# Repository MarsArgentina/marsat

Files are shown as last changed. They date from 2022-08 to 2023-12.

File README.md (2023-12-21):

# MARSAT

Marsat is an open source project aimed at developing a platform to send student experiments to the upper atmosphere. It's intended to provide it's users the following functionalities:

* GPS tracking

* APRS telemetry

* Flight computer

* Flight termination system

* Parachute

* Battery and energy management

* Bi-directional 900 MHz data link

Experiments are mounted in the upper half of the structure and must comply with 1U cubesat dimmensios. 

The system can provide conectivity and power for up to two 1/2U experiments. 

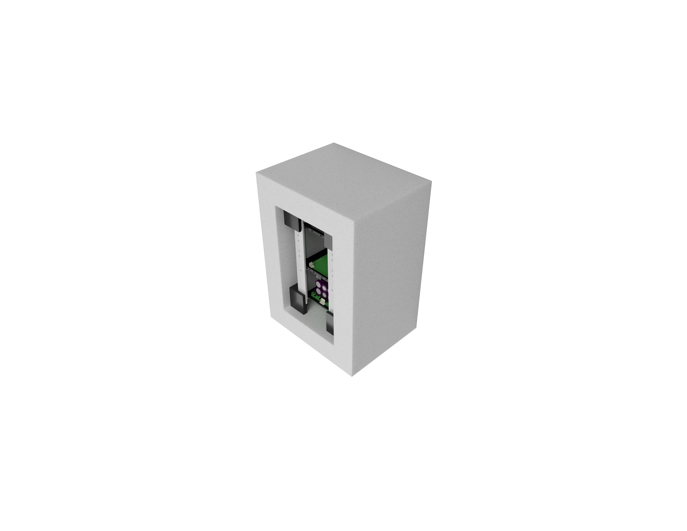
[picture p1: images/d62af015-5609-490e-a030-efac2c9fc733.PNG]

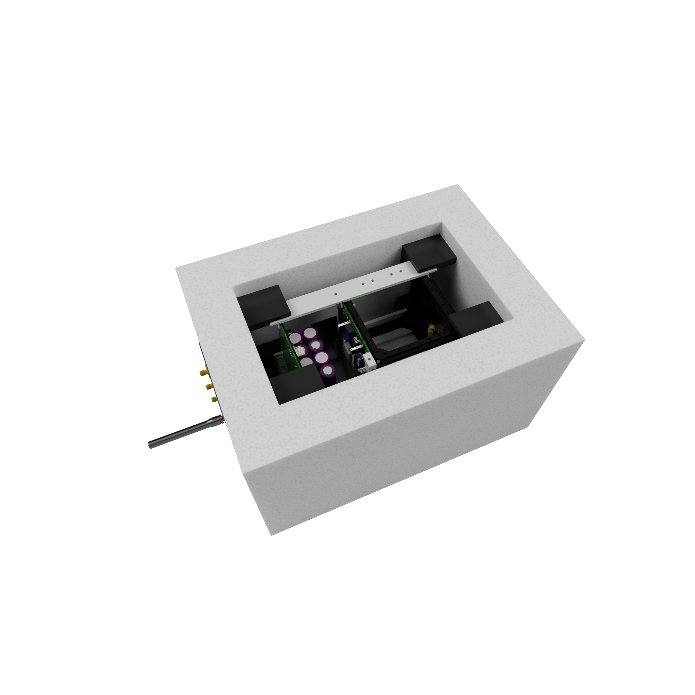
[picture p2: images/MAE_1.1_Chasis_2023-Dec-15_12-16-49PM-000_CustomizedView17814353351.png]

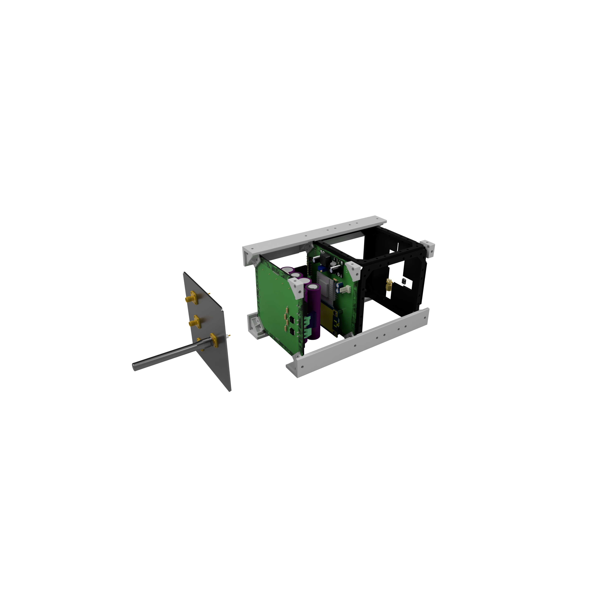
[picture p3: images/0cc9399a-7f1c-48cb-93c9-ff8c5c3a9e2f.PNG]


# Launch and Results 

Balloon was launched on December 16 of 2022, flying to 14KM until the on board computer termiated the flight due to excedinbg the configured geofense. 

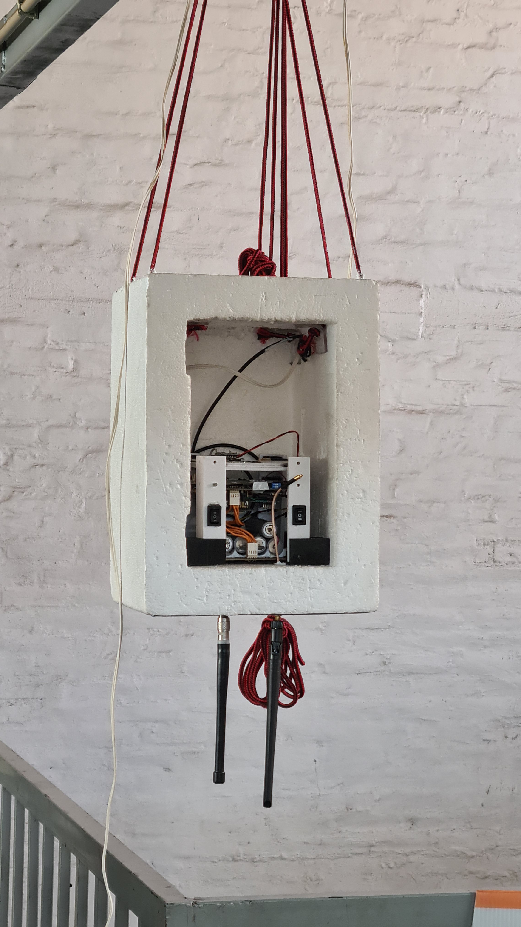
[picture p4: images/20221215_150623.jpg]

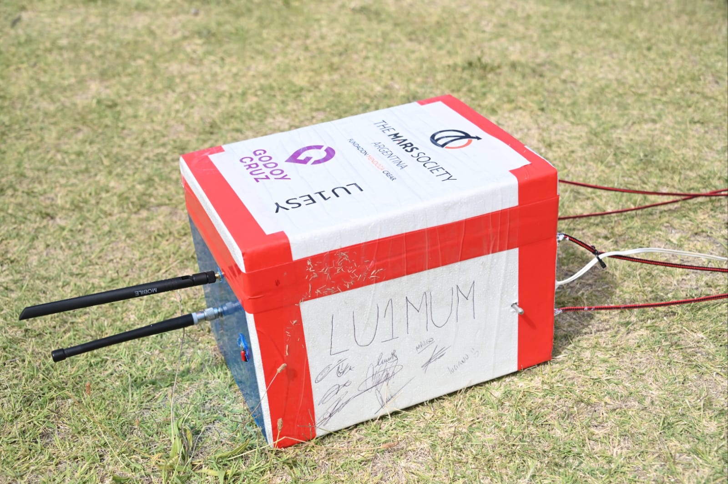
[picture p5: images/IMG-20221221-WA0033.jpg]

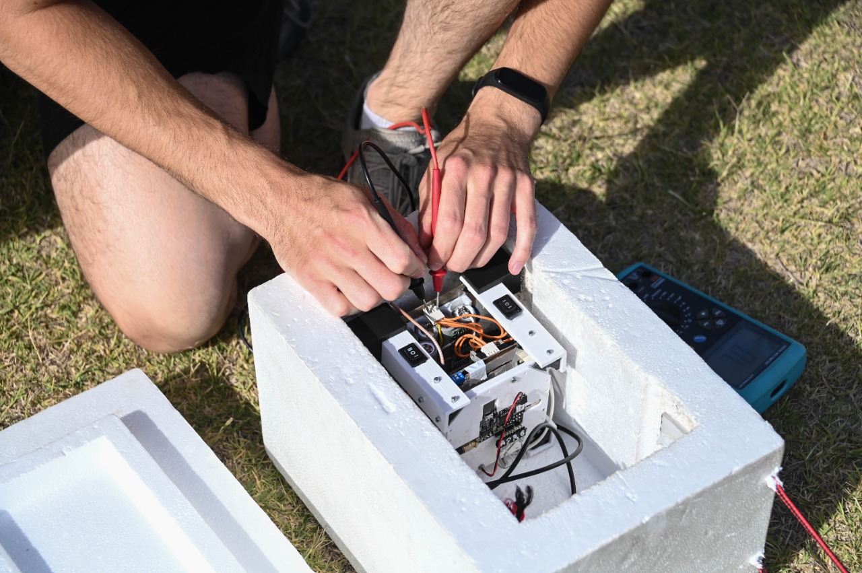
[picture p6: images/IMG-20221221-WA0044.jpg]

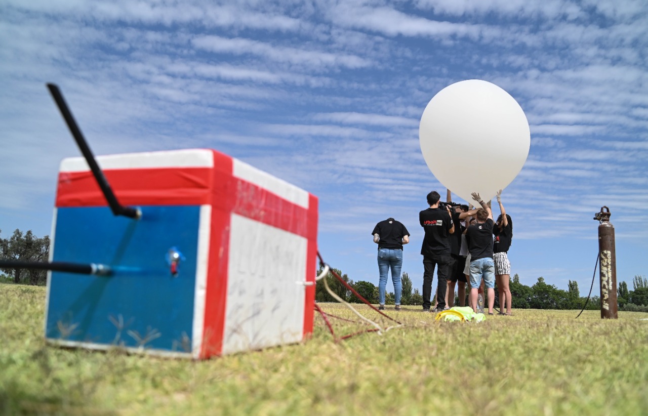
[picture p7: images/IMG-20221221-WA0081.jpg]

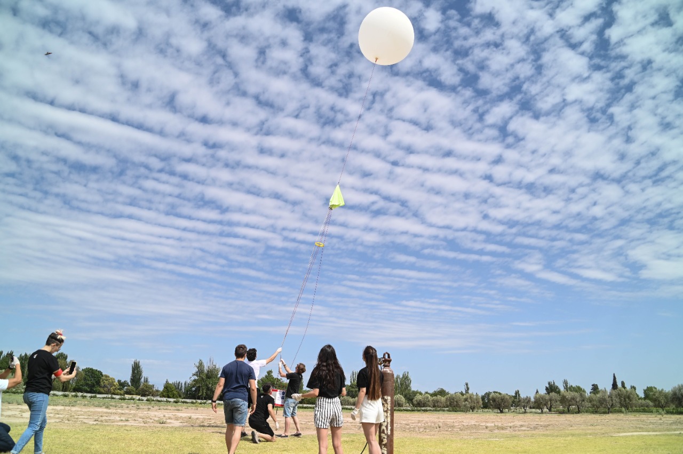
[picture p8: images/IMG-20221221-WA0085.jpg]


Some aquiered data:

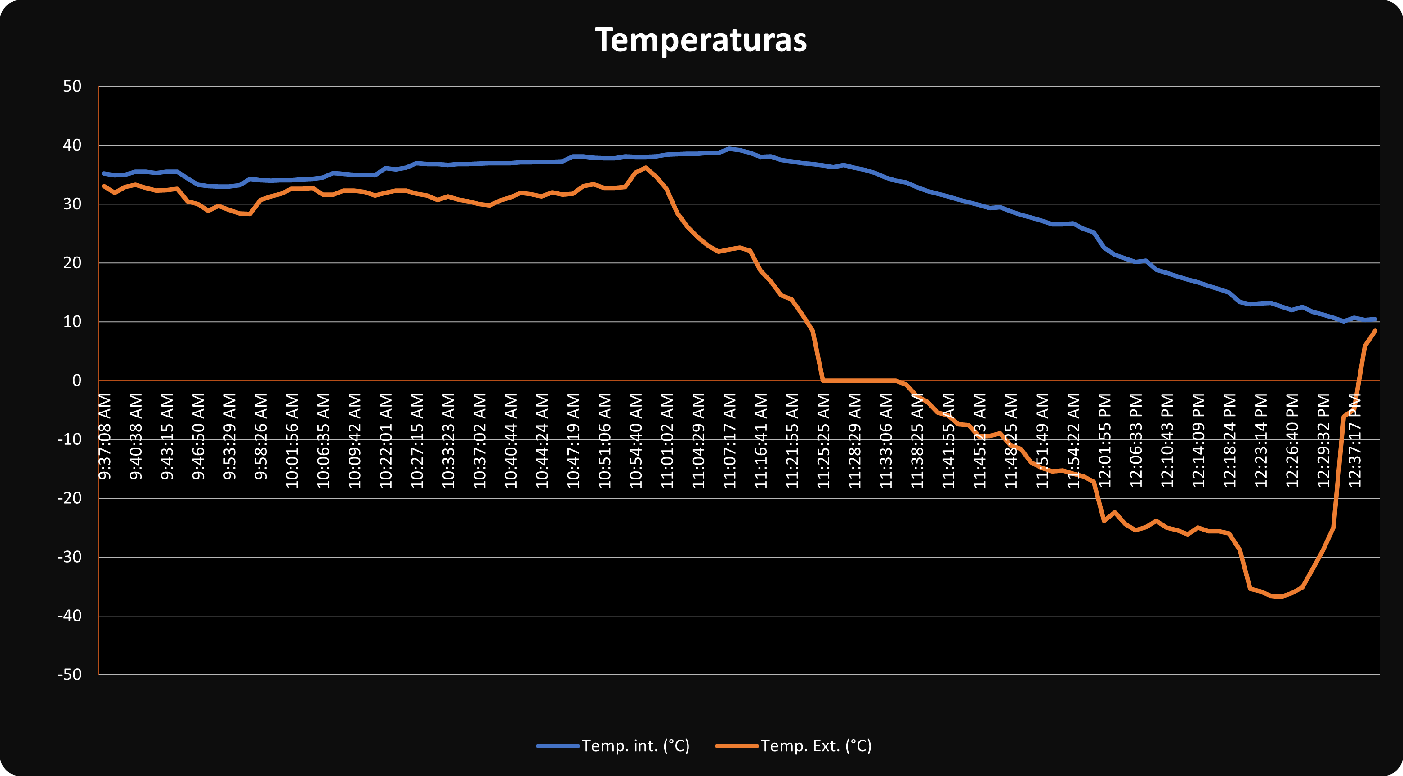
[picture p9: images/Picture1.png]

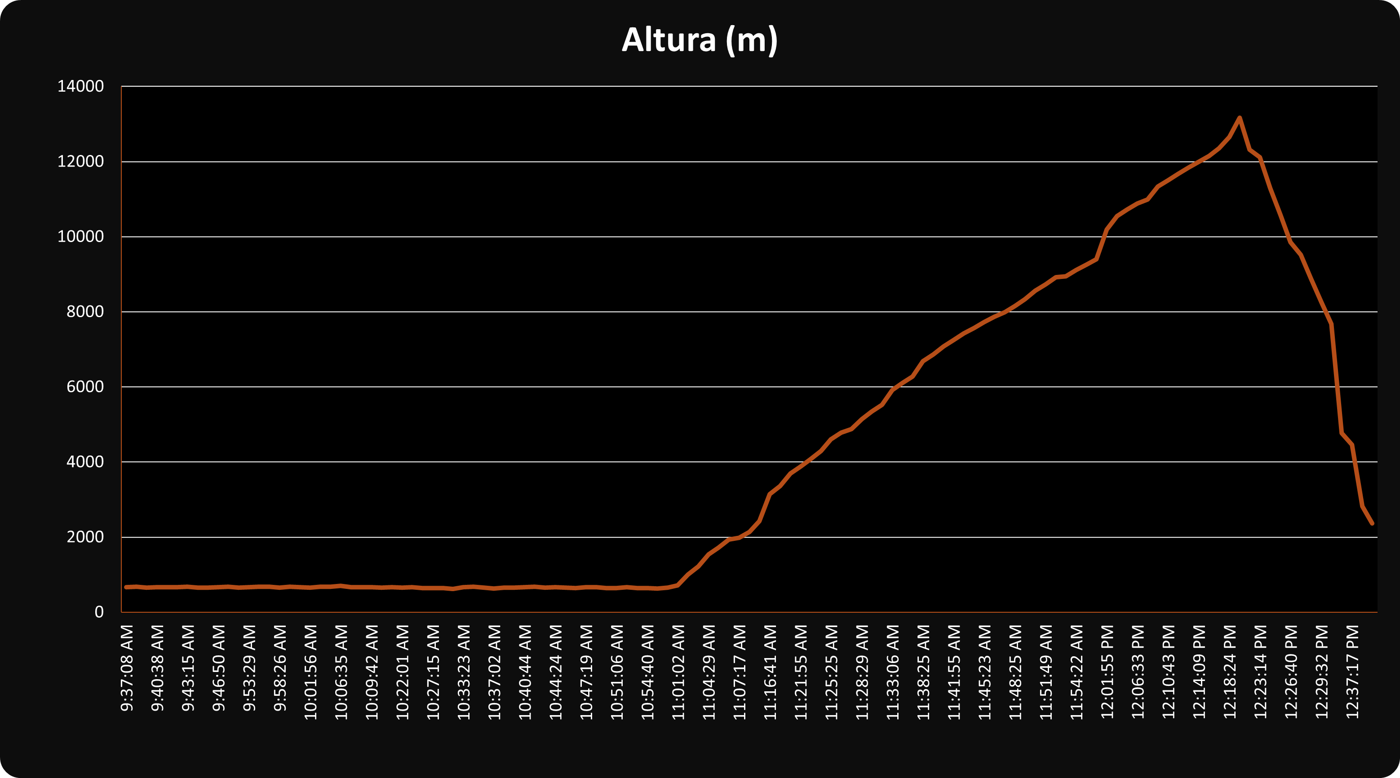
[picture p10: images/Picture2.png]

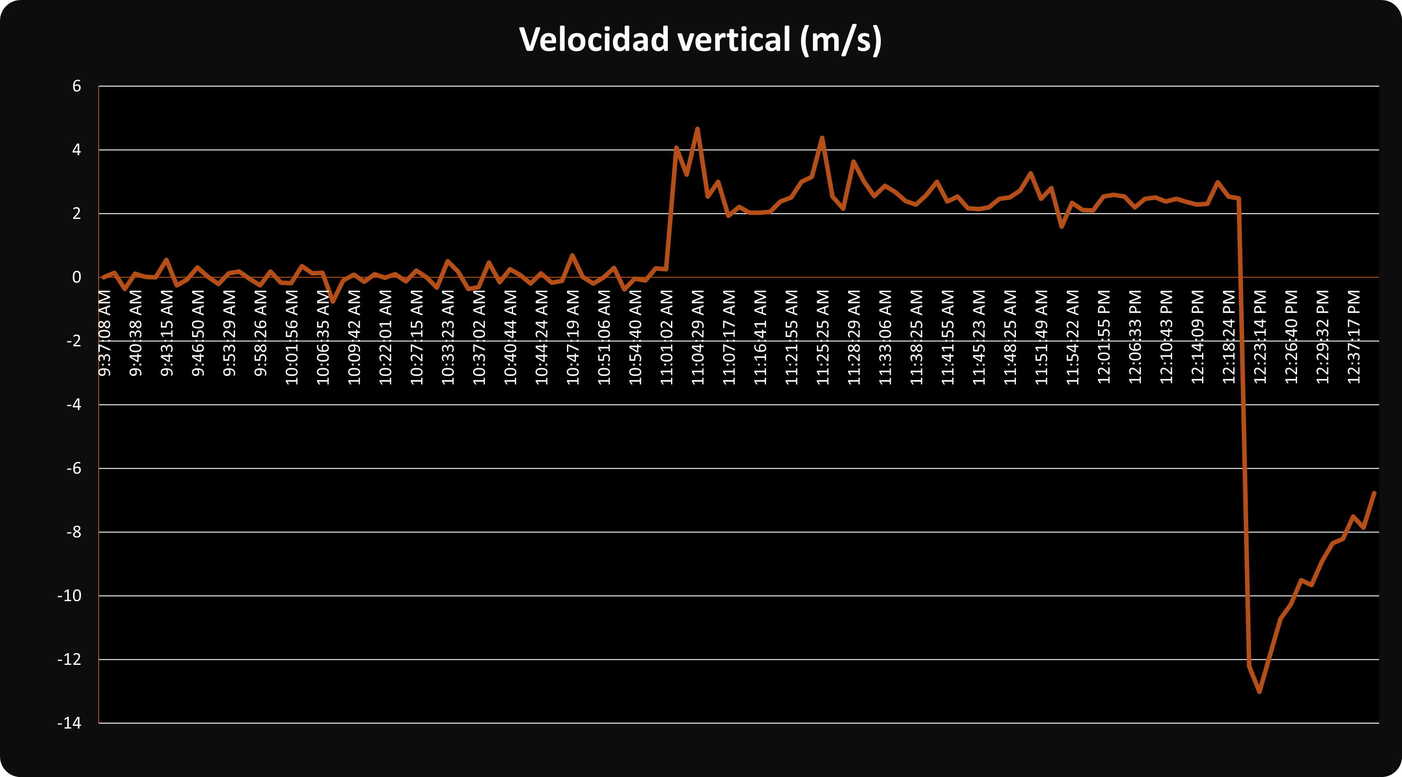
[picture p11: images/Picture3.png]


Development continues in https://github.com/MarsArgentina/TRXCAN

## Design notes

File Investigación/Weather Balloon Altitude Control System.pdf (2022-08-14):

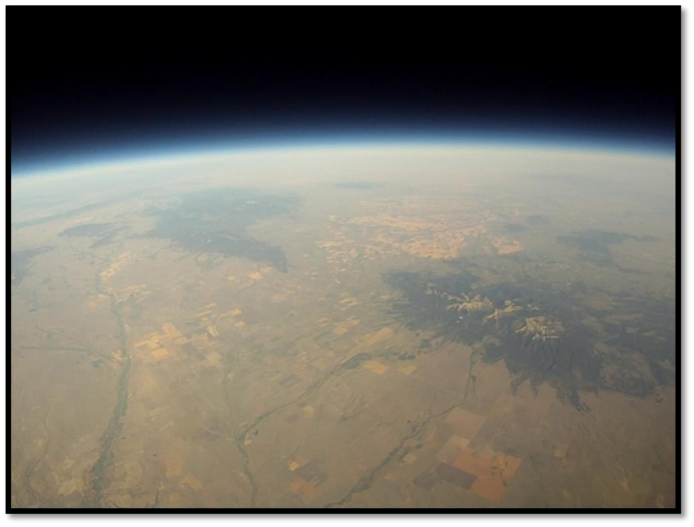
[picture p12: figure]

### Weather Balloon Altitude Control System

Senior Design 2014-2015

Tim Basta, Scott Miller, R Trevor Clark

Advisors

Randy Larimer, Berk Knighton

Sponsor

Montana Space Grant Consortium

Executive Summary

The field of high altitude ballooning is an effective and relatively inexpensive way to deliver

scientific payloads to the upper atmosphere for data collection. High altitude balloons can be

grouped into two main categories: zero pressure and burst. The burst balloon is designed to ascend

constantly until it reaches a certain altitude, at which point it will burst allowing the payload to

descend back to the ground. The zero pressure balloon is much larger, and is designed to ascend to

a certain altitude, then float until the flight is terminated. The zero pressure balloon is more

versatile than the burst balloon as it can float at neutral buoyancy for extended data collection. The

burst balloon is significantly less expensive so it is commonly used by facilities that use

meteorological sounding packages and university ballooning groups with smaller budgets. The Goal

of the altitude control system is to provide the ability to fly the lower cost burst balloon at neutral

buoyancy. This will allow users to collect data on a floating platform without the increased expense

of a zero pressure balloon.

Table of Contents

Problem Definition | 4
Functional Analysis | 12
Alternatives Evaluation | 19
Project Planning | 28
Concept Development | 33
System Architecture | 46
Detailed Design | 58
Analysis and Test | 79

Problem Definition

Introduction:

University level ballooning programs and stations that collect meteorological

sounding data typically use relatively inexpensive latex weather balloons to transport their

payloads to high altitudes. These balloons are made to fly to a high altitude and then burst,

providing no control over the duration of flight and the altitude of data collection. For

longer duration flights, zero pressure balloons are typically used. These balloons are many

times more expensive than latex weather balloons. The goal of this project is to develop a

low cost alternative to zero pressure balloons that will still provide neutrally buoyant

flight. To accomplish this goal we will develop a valve that is user controlled that can be

inserted into the neck of the latex balloon, then can be opened to vent helium and therefore

control the altitude and duration of the flight.

The mechanical portion of this project will consist of a flow tube that will be

connected to the fill nozzle. This flow tube will feature a mechanical gate vent system to

allow Helium to be vented from the balloon during flight. The mechanical valve gate will be

located at the bottom of the flow tube. this device will also have a fill port that will interface

with the fill station, to allow the balloon to be filled with Helium after attachment to the

device. The circular valve gate will actuated by a small motor, which will be controlled by

the onboard microcontroller.

The electrical portion of the project will consist of multiple control and wireless

communication systems working together to give the user control of the flight and facilitate

various in-flight experiments. One control system will be connected to the mechanical valve assembly which will control the motor which opens and closes the valve, wireless

communication with the main command capsule, and reads various sensors. A second

control system in the main command capsule will act as the main communication and

control hub for the flight system. This module will consist of a microprocessor which will

wirelessly control the valve system and interface with the users onboard long range

tracking and or communication system. Research will be performed on which

microprocessors and wireless protocol will best suit the project. Custom printed circuit

boards and supporting electronics will be designed for each module.

Needs Description:

University level ballooning programs and stations that collect meteorological

sounding data typically use relatively inexpensive latex weather balloons to transport their

payloads to high altitudes. These balloons are made to fly to a high altitude and then burst,

providing no control over the duration or altitude for data collection. For longer duration

flights, zero pressure balloons are typically used. Zero pressure balloons provide a long

flight duration at a near constant altitude. However, these balloons are many times more

expensive than latex weather balloons, which puts them out of reach of smaller ballooning

groups. This design will seek to develop a system to use burst latex balloons in place of zero

pressure balloons. This will be done by developing a valve that can be inserted into the

neck of various sizes of latex balloons to vent helium sufficient to achieve neutral buoyance

at a user controllable altitude. This will reduce the cost associated with doing experiments

that traditionally required a zero pressure balloon.

Currently the only group that has successfully done anything like this is in the past,

outside the military, is the BOREALIS program at MSU. BOREALIS has made a prototype to

vent helium. The current system requires a wired connection from the vent to the payload,

this allows the user to manually open and close the vent. The improvements that need to be

made are to adapt this system for traditional 2000 and 3000 gram latex balloon as well as

smaller 200 gram balloons used for weather sondes. The main things that need to be

improved are making a valve design that can be used for weather sondes and for larger

2000 or 3000 gram weather balloons, wireless communication between the valve and the

main payload, and the valve needs to have the ability to autonomously open and close to

achieve neutral buoyance at a user selectable altitude. Using a valve will reduce the cost

associated with doing experiments that traditionally required a zero pressure balloon.

Being able to wireless communicate with the valve will reduce possible complications such

as the wire connected to the valve getting tangled with the parachute. Wireless

communication between the valve and the main payload will further reduce the weight of

the system. Having the valve autonomously navigate to a desired height will reduce human

error and the need for communications between the ground and the balloon during flight.

This system will allow for a broader range of experiments at smaller university level

ballooning programs to be done at relatively low cost. Particularly this will provide a stable

camera platform for the BOREALIS program to record the 2017 eclipse. Another important

application of this system will be for use with weather sondes in extreme weather

situations, such as hurricanes. This is will be beneficial because it will allow weather

sondes to collect data for longer periods of time and at selectable altitude. This will reduce

cost and risk of using aircraft to take these measurements.

Stakeholder List:

A low-cost controllable-altitude balloon platform has a diverse group of stakeholders. The

stakeholders include the students and campus faculty involved in the program, the Montana Space

Grant Consortium, and the atmospheric science community. Each stakeholder has a unique vested

interest in the completion of this project as detailed below.

The primary stakeholders are the students and campus faculty directly involved in the

program. The students responsible for the project have a vested interest in its completion as it

fulfills a graduation requirement for their respective majors. The project also offers them valuable

engineering design experience to take with them to their future employer. The campus faculty are

also stakeholders in the project’s success. Not only are the faculty asked to help guide their students

towards successful completion, they are also ultimately responsible for assigning grading marks for

the student’s work as well. The faculty are also invested in the program to help further Montana

State University’s reputation of producing excellent engineers.

The Montana Space Grant Consortium (MSGC) BOREALIS program is a stakeholder in this

project as they are the organization sponsoring the student’s work. MSGC is interested in a

controllable-altitude balloon platform for their 2017 total solar eclipse project which hopes to take

live images of the total solar eclipse from the stratosphere. A reliable altitude control system for

their balloon payload is essential for placing their cameras at the correct altitude to capture the

eclipse.

Finally, the atmospheric science community will greatly benefit from this system. Scientists

currently use latex weather balloons to measure atmospheric and weather phenomena using

measurements obtained as their balloon payload rises through the atmosphere. Once their payload

reaches a certain altitude it bursts, terminating their flight and experiment. An altitude control system (such as that being developed in this project) would allow more measurements to be taken

before the flight is terminated as the balloon could loiter at a specific altitude without bursting.

In conclusion, the stakeholders include:

- Students and faculty involved in the project
- Students directly involved in the design, build and testing of the project
- Campus faculty supporting and grading the students
- Montana Space Grant Consortium
- MSGC BOREALIS program requiring a stable camera platform in the stratosphere for

their eclipse project

- Atmospheric Scientists
- Scientists involved in measuring atmospheric conditions

Project Goals:

The main goal of this project is to provide a system that will allow users to fly payloads at

neutral buoyancy using latex weather balloons (Burst balloons). This system will be required to

vent the correct amount of Helium from the balloon within the time constraints of the balloon

mission. This system will also be required to restrict the flow of Helium adequately enough when

closed to eliminate variability in the float altitude. The two sub-goals for this project include

autonomous vent control, and short range wireless control of the Helium vent. The autonomous

vent control will be an electronic function built into the valve itself. It will have a user interface for

selection of float altitude, and a microcontroller that will make vent decisions based on the user

selection. The short range wireless control will give the user the ability to control the valve

manually by using another long range communication system on a different payload container on

the same payload chain. For example: the user would send the 'open vent' command through their

standard communication system (e.g. amateur radio or satellite modem), the command would be received by their payload chain attached to their balloon, and the command would be transmitted

short range from the communication payload to the valve system.

Project Constraints:

The constraints placed on a high-altitude weather balloon system include project length,

cost, weight, density, breaking force, temperature, endurance, size, and communications. A detailed

look at these constraints is provided below:

- Time
- The project must be completed within the two semester Senior Design sequence

specified by Montana State University

- Cost
- The project must be completed within the budget assigned to the student group by

MSGC

- Actual dollar amount is yet to be determined
- Weight
- Valve and control systems must be as light as possible to allow other systems to

utilize the total weight allowed (see below)

- FAA regulations (FAA Part 101 – (a)(4)(ii) and (iii)) require no more than six

pounds per payload, and no more than 12 pounds overall total for multiple payloads

- Density
- FAA regulations (FAA Part 101 – (a)(4)(i)) specify an upper maximum density of

three ounces per square inch to avoid catastrophic aircraft damage should a

collision occur

- Determined by dividing the total weight in ounces of the payload package by

the area in square inches of its smallest surface

- Breaking force
- FAA regulations (FAA Part 101 – (a)(4)(iv)) require that any rope or suspension

used for the payload must break free with an impact force of no more than 50

pounds

- Payload must survive impacts with the Earth once the flight terminates
- Parachute system must reduce speed to 10-20 feet per second depending on

payload / experiment requirements

- Temperature
- All systems must be able to withstand temperatures from -60⁰C in the upper

atmosphere through +35⁰C at the Earth’s surface

- Mechanical and electrical systems must operate through this range for extended

periods of time as indicated in the endurance section

- Endurance
- Both mechanical and electrical systems must be able to operate for the duration of

the mission

- Typical BOREALIS loiter flights (“zero pressure flights”) last approximately 3

hours

- Typical BOREALIS flights require that any flight systems are operational 30

minutes before balloon launch

- Size
- While there are no size constraints directly placed on the valve and control systems,

they must conform to the weight, density, and breaking force specifications

provided above

- Communications

- Control system must be able to interface and communicate with the current

BOREALIS communications payload which includes an NAL Research 9602-LP

Iridium satellite modem connected to an Arduino Uno microcontroller

- Communications protocol / interface can be determined by the designers

Functional Analysis

Introduction:

The following functional specification overviews the high level requirements of the valve

control system. Very few if any technical details will be provided however the overall function of

the system will be detailed. The functional specification starts with a black box model which

describes what each individual subsystem does along with a high-level look at how the systems are

connected together. The next section is functional specifications. The functional specifications

provides a granular look at what each subsystem must do to accomplish the overall goal of the

project. Each high level function is broken down into smaller sub functions as needed. Finally the

design metrics for the project will be presented. The design metrics are the overall design goals that

the end product will be weighed against to determine if the project was successful or not.

Black Box Model;

This project consists of four main subsystems, the preexisting long range communication

system, an Iridium satellite modem, a controller in the main payload to interface to the Iridium

satellite modem, a controller up on the valve with a GPS unit, and the a valve to vent helium.

Currently the MSGC BOREALIS program is using an Iridium satellite modem to communicate with

the balloon payload other ballooning groups commonly use amateur radio DTMF. This project will

entail designing a main payload controller that can interface to an existing communications system

be that a satellite or amateur radio DTMF. This controller will then via a wireless connection

communicate with a controller up on a valve closer to the balloon. This valve controller will then

directly control a valve that is inserted into the neck of a balloon which will open and close enabling

or restricting the flow of helium out of the balloon to achieve neutral buoyance. The valve controller

will also have the functionality to operate autonomously, venting helium to achieve neutral

buoyance at a preprogrammed attitude. It will do this be implementing an algorithm to interpret

GPS data and determine when and for how long the valve should be opened to achieve the user

selected altitude.

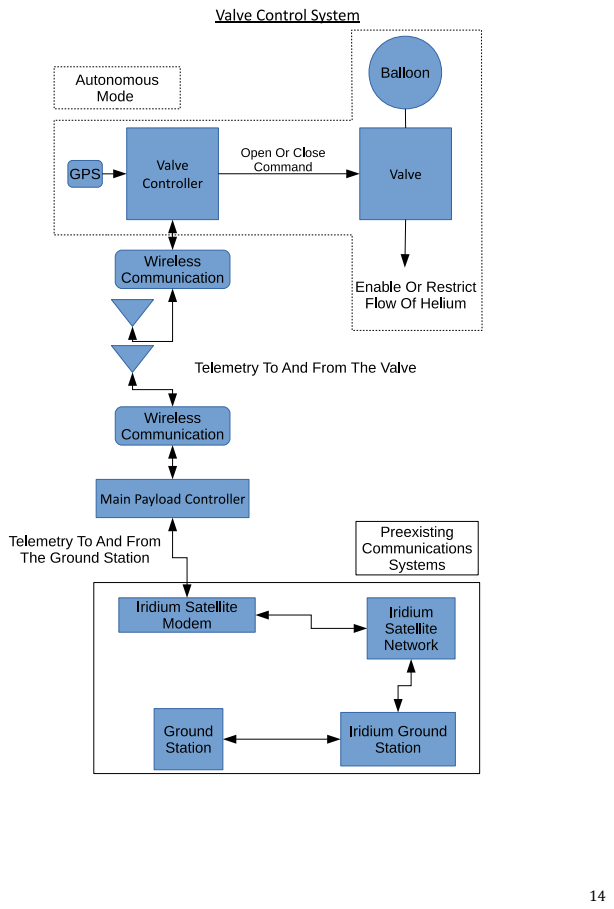
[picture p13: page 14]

Functional Specifications:

The purpose of the valve system is to allow users of latex high altitude balloons to fly them

at neutral buoyancy. This will be accomplished by venting a certain amount of helium out of the

balloon during flight to affect the amount of lift produced by the displaced air. This will allow users

to extend the duration of their flights, and allow them a degree of control in flight duration and

altitude.

The electronics package will consist of two functional subsystems: a control subsystem and

a valve subsystem. The control subsystem will reside within the main payload container that the

end user supplies. The control subsystem is responsible for interfacing with the end user's tracking

and command system (Iridium satellite modem, amateur radio, etc. ) The interface protocol will

need to be well documented for easy integration with the end user's existing payload. The interface

will allow for remote control of the valve and its various functions. The control subsystem must

wirelessly communicate with the valve subsystem. The control subsystem must have an endurance

of 6 hours.

The valve subsystem interfaces directly with the valve mechanics and is responsible for

actuating the valve as required. A wireless connection must be established between the control

subsystem and the valve subsystem if required. The valve subsystem must also have a autonomous

mode which works independently of the control subsystem if activated. The autonomous mode will

use internal logic and various sensors to determine when to actuate the valve mechanics. In either

mode the valve subsystem must be able to wirelessly send status updates and sensor readings to

the control subsystem.

Specific design requirements for this project are as follows:

- The valve system will be required to have a sufficiently high flow rate to allow the user to

bring the balloon to float (Neutral buoyancy) within 15 minutes of being open. Due to the

ascent rate of the average high altitude balloon flight, the time window for venting is limited

to a maximum of 15 minutes. If the vent time takes longer, the balloon may burst at high

altitude due to excessive volume.

- The valve system will be required to achieve float at a pre-specified altitude to within a 10%

degree of accuracy. This design requirement is aimed at making this product marketable to

institutions that collect meteorological sounding data that will require altitude control that

is acceptably accurate.

- The valve system will be required to operate inside the temperature range of -60 C to 40 C.

This is the average operating temperature range from ground level to 100,000 ft.

- The valve system will be designed for use with 300 gram Kaymont brand balloons. Future

designs may include a design that is compatible across other brands or sizes of balloons, but

this project will be designed for a balloon commonly used for meteorological data

collection.

- The total weight of the valve system cannot exceed 8 oz. The 300 gram balloons commonly

lift a 2 lb. payload, and the addition of a valve system weighing more than 8 oz. becomes

unreasonable compared to the average payload weight.

- Communication specification for interfacing the valve system with the end user's payload
- The valve system is not required to control or track the end user's payload, however

a data link protocol is provided to interface with the user's system if desired. The

protocol specifies the method of communication the valve system expects from the

external control system such as baud rate, serial protocol, timing, etc.

- Battery endurance of 6 hours

- The complete valve system must operate for a minimum of 6 hours, however no

particular power usage specification is required as long as the other functional

specifications are still met (temperature range and weight would likely be most

affected). The valve system design must determine how best to achieve this goal

through efficiency of operation, battery capacity, DC/DC converter requirements,

sleep states of the microprocessor, etc. The 6 hour requirement is based on the

intended use of the end product.

- Cost per unit less than $100 for 100 units.
- Due to the average cost of weather sounding packages, it would be unreasonable to

expect a customer to pay more than $100 for the neutral buoyancy upgrade.

- The valve system will be required to provide flight termination for the balloon by venting a

significant volume of Helium to cause the balloon to descend back to ground level.

- The valve will be required to have an in-line fill system that will allow the user to attach the

balloon to the valve prior to fill, then inflate the balloon with Helium through the valve. This

system will also require a fill station that will interface with the Helium tank regulator.

- This project will be required to be accomplished within 3 test flights and 1 demonstration

flight due to budget and time requirements.

Design Metrics:

The design metrics for the project are the most important project goals that must be met for

the project to be a success. These specifications are the most important high level goals as they are

the specifications given to the project group by the end user. If these design metrics are not met the

end user will not only be displeased, they may proceed with another company's product.

The design metrics for the project are specified as follows:

- The valve mechanics must be simple to connect the latex weather balloon to and also hold

onto the balloon so it does not disconnect in flight.

- The valve mechanics must allow for inline fill of the latex weather balloon.
- Inline fill allows the end user to attach their latex weather balloons to the valve

mechanics and then connect their helium supply to the valve. The valve system must

not be cumbersome to connect or interface with.

- A float altitude between 30,000-60,000 feet within a 10% tolerance must be achievable with

the system.

- This altitude range encompasses the altitude regions in which the end user would

typically utilize such a system, and an acceptable tolerance level at those altitudes.

- The valve must weigh no more than 1/2 pound.
- If the valve system is heavier than that specified the end user will lose valuable

payload weight for their experiments.

- The entire system must cost no more than $100 per unit in 100 unit quantities.
- To be competitive or desirable with the intended market the entire valve system

must not cost more than the cost of a typical weather balloon ($100).

- Up to three test flights and one final flight may be used to test the project design.

Alternatives Evaluation

Introduction:

This section of the report will cover the design alternatives proposed by the Capstone

group. These design alternatives are a group of ideas that could possibly be used to accomplish the

functional requirements. This report will discuss the design alternatives in detail, then rank them

based on operational criteria proposed by the Capstone group. This report will also discuss the user

operation requirements for the project. These can include ergonomics, setup, maintenance, and

correct operation of the product.

Design Alternatives:

The design alternatives area is where you will be explaining the top design selections that

you have come up with. Here, about a 1 – 1 ½ pages for each design idea along with sketches needs

to be produced so the reader can get a good understanding of what the concept is. The sketches

don’t have to be perfect. You can make copies of the ones in your journal and scan them in.

Mechanical design alternatives:

Diaphragm valve: This design alternative will obstruct the flow of Helium through the vent tube

with a flexible rubber disk trapped against a ridge internal to the flow tube. Venting will be

accomplished by an armature pushing on the diaphragm from the outside, temporarily

compromising the seal and allowing the Helium to vent.

Butterfly Valve: This design alternative will use a disk of rigid material connected through the

center axis by a rotating connection point. The inside of the flow tube will have a sealing ridge on

half of the circumference, and have an identical sealing ridge on the outer opposite side. The flow

would be obstructed by having the disk rotated about the pin until it contacts the stops. Helium

flow will be allowed by rotating the disk in the opposite way.

Circular gate Valve: This design will use two circular disks of rigid material that lay flat against one

another and cap off the end of the flow tube. Each disk has as identical and symmetrical hole

pattern such that when the openings are lined up, gas is allowed to flow through the openings. By

rotating the top disk, the openings are misaligned, and the flow opening is closed. The two disks

will use a high viscosity lubricant at their interface. This will help make the seal gas tight, as well as

prevent the two surfaces from wearing on one another.

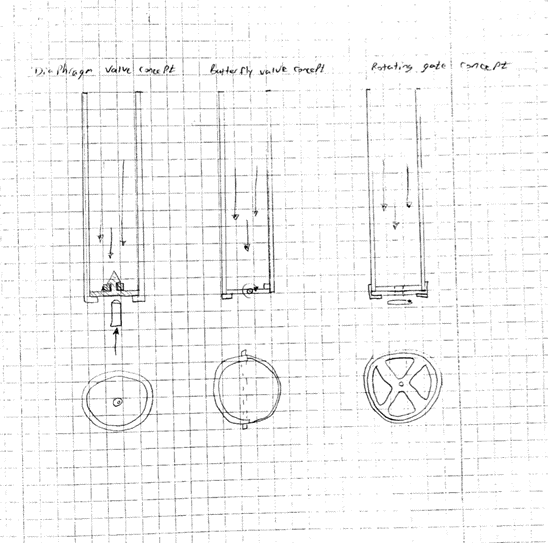
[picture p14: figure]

Electrical Design Alternatives:

Design Alternative 1: Microprocessor with external short range radio.

This alternative is using a microprocessor with an external short range radio module, such as an

Xbee ZigBee module.

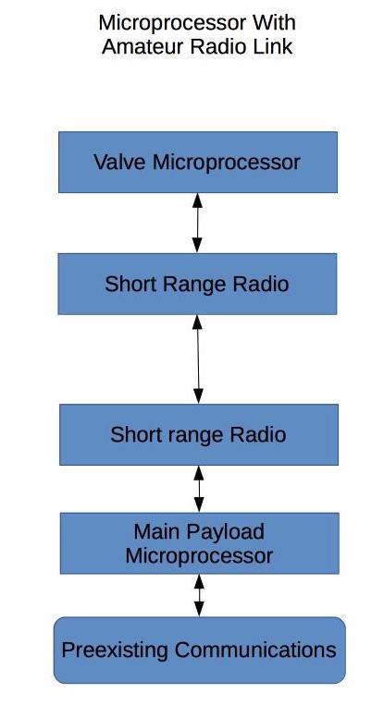
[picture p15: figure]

Design Alternative 2: Microprocessor with amateur radio link.

This is probably the most commonly used solution to this design challenge however there are a lot

of things to interface together and it is somewhat complicated.

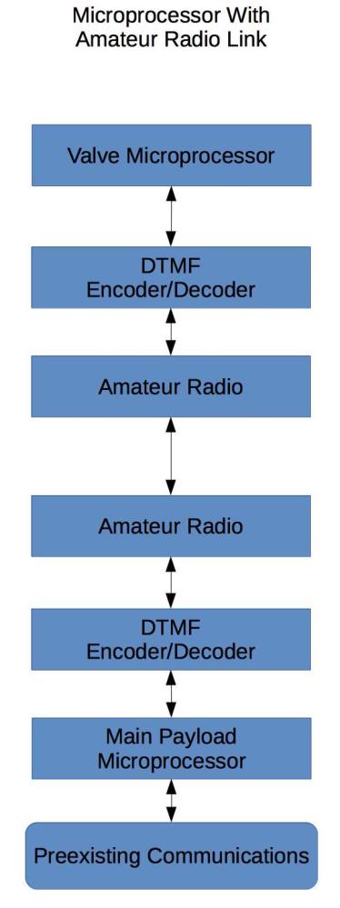
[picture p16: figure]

Design Alternative 3: Microprocessor with integrated short range radio.

There are some microprocessors that have integrated radios similar to ZigBee modules. This

system will have the least amount of components

Client/User Operation:

The client and user operation of the valve has both mechanical and electrical considerations

and will be explained in detail individually.

Proper operation of the physical valve and related components is vital to the end user

successfully deploying the system. There are complexities associated with integrating the system

with the end user’s tracking and communication system as well as with connecting and filling the

necessary weather balloon. Easy to follow instructions and methods to reduce incorrect usage will

be vital for preventing errors and avoiding unnecessary confusion and frustration.

The valve system will require an interface on the outside of the flow tube that will allow the

user to easily and quickly connect the specified balloon type to it. This will be either a surface that

provides enough friction to retain the balloon nozzle, or a latching system that will capture it.

The valve system will also need an in-line fill system that will allow the user to fill the

balloon with Helium through the valve system after it has been connected. A unique fill nozzle that

can interface on one end with the Helium tank regulator, and on the other end with the valve, will

need to be created. This will allow the user the most efficient launch procedure, instead of having to

fill the balloon then attack to the valve.

The electrical and computer user interfaces are also important components of the valve

project. The electrical operation considerations will be detailed separately from the computer user

interface. Electrical operation includes the specification for interfacing the end user’s

communications equipment with the valve microprocessor. The computer user interface is used to

select the valve’s operating mode as well as for downloading sensor and operation data.

The user interface for the electrical system describes how the end user will interface their

communications system with the microprocessor within the valve system. Because the valve

system must interface with a wide range of tracking and communication systems, a protocol

standard must be developed and documented. This document will specify how to physically

interface with the valve microprocessor, electrical specifications for logic levels, and how data is

expected to be sent and received. The specifications for the physical connection with the device

must include port pin-out diagrams, special handling requirements (such as static electricity

precautions), and where to find the ports on the printed circuit board. The electrical specification

must include maximum and minimum electrical ratings, supported logic levels, and timing

requirements. Finally the protocol which is used to communicate data to and from the valve

microprocessor must be detailed (such as how and when to acknowledge a data byte).

The computer user interface will be used to both upload operating information to the valve

microprocessor and for downloading data stored in its onboard storage. A graphical user interface

should be used to easily perform these actions which can be run from either a software application

or a specially crafted webpage. If any features are not self-explanatory a user manual or electronic

help document should be present to guide the end user through the operation. The interface will

allow the end user to select modes of operation such as fully autonomous mode, a desired altitude

ceiling, what sensors to record data from, and/or if the valve should expect commands from the end

user’s own communication equipment mid-flight. The interface must also allow for downloading

flight information after the flight has concluded. The user interface must present this data in an

easy to work with file format such as comma separated values within a text file.

Decision Matrix:

Using a design matrix the best solution for the design challenge can be selected via

quantifiably criteria. In a design matrix on the left the different design alternatives are listed and

then along the top of the matrix the different design criteria are listed. Then the design alternatives

are systematically scored on a scale, in this case we are using a scale from 1 to 5 with 5 being the

best, against the selected criteria. For this design the selected criteria are power usage, cost

effective, ease of integration, durability, ease of use, and overall effectiveness. Power usage is

probably the most important criteria for this project. This is because low weight is a critical

requirement for the ballooning payload. More power usage means more batteries which translates

into more weight. Cost effective was chosen as a criterion because the final design needs to cost less

than $100 per unit for 100 units. Ease of integration with the rest of the system and ease of use for

the end user are obviously important because if it is too difficult to use no one will want to buy or

use the product. Durability of the design also translates to the lifetime of the product. A longer

product lifetime increases the value for the end user. The design alternatives were also scored for overall effectiveness in meeting the design requirements for this project. The design matrix

generated is shown below with total scores for each design alternative in the far right column.

Criteria Scale: 1-5 With 5 Being the Best | Power Usage | Cost Effective | Ease of Integration | Durability | Ease of Use | Overall Effectiveness | Total

Design Alternatives

Wireless System

Microprocessor and Short Range Radio Separate | 3 | 3 | 5 | 3 | 5 | 5 | 24
Microprocessor And Amateur Radio With DTMF | 1 | 1 | 3 | 3 | 4 | 5 | 18
Microprocessor With Built In Short Range Radio | 5 | 5 | 2 | 5 | 1 | 5 | 23

Mechanical System

Diaphragm valve | N/A | 5 | 2 | 1 | 3 | 1 | 12
Butterfly Valve | N/A | 3 | 3 | 4 | 4 | 3 | 17
Rotating Gate Valve | N/A | 4 | 5 | 5 | 5 | 5 | 24

From the above design matrix the winning design alternatives for the electronics system is

microprocessor with a separate short range radio module, and for the mechanical system the rotating gate valve. These designs are superior to the other alternatives when compared with the

selected criteria.

Project Planning:

Introduction:

This report will detail the Project planning for the Weather Balloon Altitude Control

system currently being designed. This report will contain risk analysis information that

covers the severity and probability of the failure modes possible for this system. Next,

plans for mitigating risk items above the design threshold will be detailed. A brief

breakdown of the work structure for the project will also be included. This will cover high

level tasks that need to be completed for the project. The responsibility matrix will assign

various design goals to certain members of the design team. Finally, the report will be

concluded with a project schedule that will include a timeline for project goal completion.

Risk Analysis:

- Open failure: The valve could fail to open on command, resulting in the balloon to rise to a

terminal altitude and burst, causing the project to fail the mission parameters and

potentially become lost.

- Flow failure: the valve could fail to vent an adequate amount of Helium to satisfy the

mission requirements.

- Close failure: The valve could fail to close after the venting cycle is completed, causing the

balloon to become negatively buoyant before float is achieved resulting in mission failure.

- Mechanical Failure: The mechanical linkage between the balloon and payload could fail,

resulting in the payload descending before mission completion.

- Communications Failure: The wireless link between the main payload and the valve

controller could fail and the ability to control the valve could be lost. This could result in the

balloon gaining excessive altitude and bursting if control is lost before burst, if control is

lost after neutral buoyance was achieved the balloon could go derelict, or if control is lost

when the valve is open the balloon could vent excess helium and land before intended.

- Autonomous valve algorithm failure: If the algorithm to come to neutral buoyance fails the

balloon will either never vent helium and gain excessive altitude and burst of, vent too

much helium and land early, or the valve may open and close undesirably.

- Code failure: Any type of infinite loop which may occur in the code would effectively

terminate the microcontroller's ability to control the valve or make other decisions.

- Electronics failure: the power system which runs the electronics could fail or short and

draw more current than intended. This could cause the microcontroller to reset, damage to

the power system or electronics, or reduced battery life.

0=lowest severity, probability | 10=High severity, probability
Risk Item | Severity | Probability
Open Failure | 3 | 2
Close Failure | 2 | 2
Flow Failure | 1 | 3
Mechanical Failure | 5 | 1
Communications Failure | 5 | 1
Autonomous Valve Algorithm Failure | 5 | 3
Code Failure | 5 | 2
Electronic Failure | 5 | 1

Mitigation Strategy: ( it was determined that none of the risk factors were unacceptable, so

mitigation strategies were created for each one, independent of a trend line)

- Open failure: This problem can be solved by appropriate tolerancing of mechanical

components, and correct execution of the autonomous vent code.

- Flow failure: This problem can be solved by increasing the effective flow area of the valve.
- Close failure: This problem can be solved by appropriate tolerancing of mechanical

components, and correct execution of the autonomous vent code.

- Mechanical Failure: This problem can be solved by applying appropriate safety factors to all

mechanical components in the system.

- Communications Failure: Thorough testing will the full system to insure there is no

interference or other unforeseen problems that would result in communications failure.

- Autonomous valve algorithm failure: In order to mitigate the risks associated with the

algorithm rigorous simulation and testing will be done to assure that the algorithm

performs as intended.

- Code failure: Full systems testing will mitigate most common code failure modes. Watchdog

timers can be used to prevent total system failure if unforeseen infinite loops occur.

Recursion

- Electronics failure: Full systems testing will mitigate any issues experienced with the

electronics design or power system. Current draw during different modes of operation will

be measured and analyzed to ensure the power system can perform as required.

Environment testing can be performed in the BOREALIS lab vacuum chamber.

Responsibility Matrix and Work Breakdown Structure:

Task | Tim Basta | Trevor Clark | Scott Miller
Valve 3D Modeling | x
Mechanical Calculations | x
Order Mechanical Components | x
Order Electronic Components | | x | x
Electronic Prototyping | | x | x
Mechanical Prototype | x
Casing Design | x
Code Development | | | x
PCB Design | | x | x
PCB Assembly | | x | x
Website Construction | | | x
Final Mechanical Systems Assembly | x
Final Electronic Systems Assembly | | x | x
Testing | x | x | x
Documentation | x | x | x

Project Schedule:

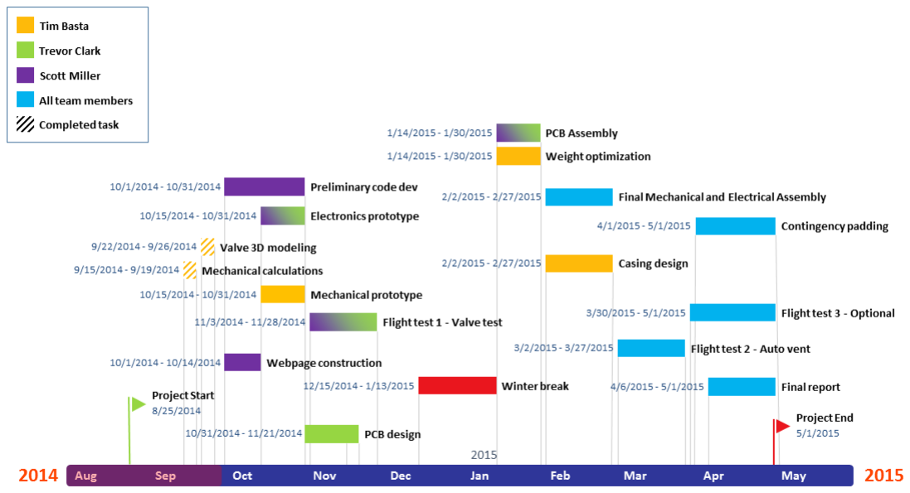
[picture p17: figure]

Concept Development

Introduction:

The design alternative that was chosen from the decision matrix is a micro-controller with

an integrated radio and a rotating gate valve. Now that these design choices have been selected

above the others they will be further explained and developed. The individual components will be

explained in greater detail along with how they integrate with the other components in the overall

system. In order to make the best overall product a number of interviews were performed to get

some feedback on how the current design could be improved and if there should be any additional

features added. In accordance with the feedback that is received the design will be potentially

changed or added to. Even though the seemingly best design has been chosen there is some

potential for some design choices to fail. In order to prepare for this possibility a contingency plan

is developed and presented here.

Concept Design:

In order to achieve the goal of developing a weather balloon high altitude control system a number

of alternatives were evaluated. The designs that scored highest in the decision matrix were a

microprocessor with a built in wireless receiver and transmitter and a valve with a rotating gate.

This is shown below.

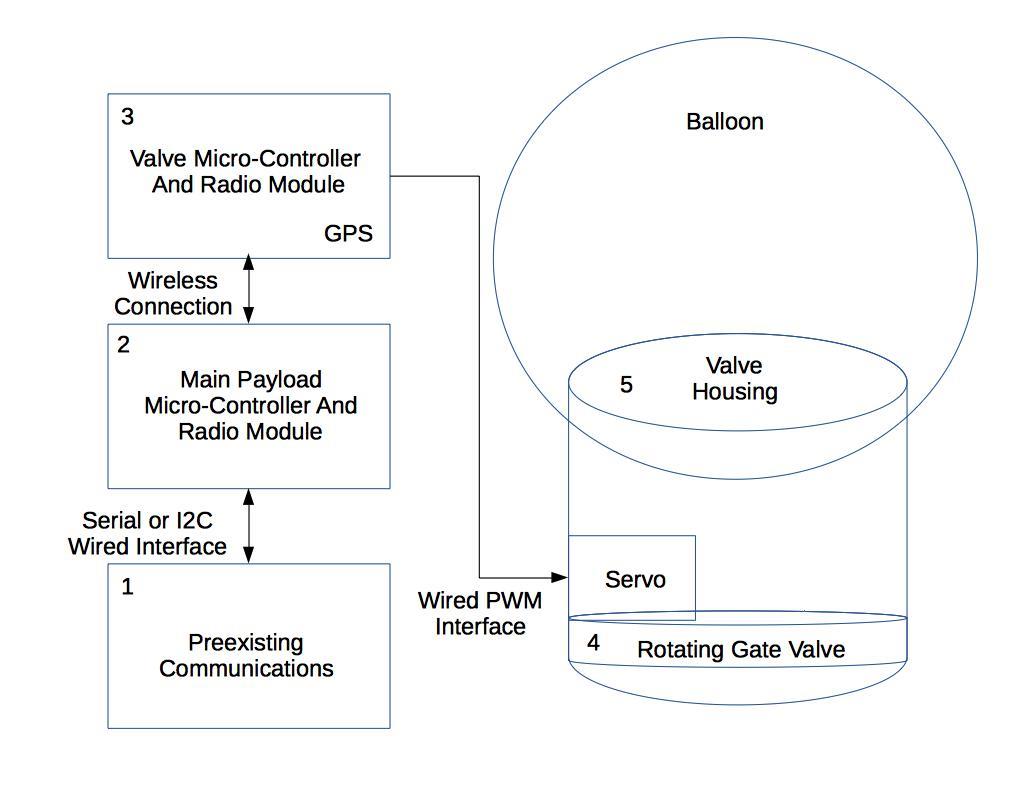
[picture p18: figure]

The following is a detailed explanation of the different components of the chosen design.

1. Preexisting Communications - This is not part of the design but is something the design will

interface with, so it is helpful to understand its function. The BOREALIS program at

Montana State University uses an iridium satellite modem for communications between a

ground station and the balloon during a flight. The ground station communicates with the

modem by sending an email to the Iridium company who then sends it via satellite to the

modem on the balloon payload. The modem has a serial connection and three digital pins

that can be interfaced with. Other ballooning groups use a variety of different options for

communicating with the balloon. Traditionally one of the most common has been using

amateur radio with a DTMF encoder and decoder which usually have a serial interface. The

goal of this design is to have a system that can be easily interfaced to whatever a given

group is using for their ground to payload communications. This will be accomplished by

having available Serial, I2C, and digital pins available.

2. Main Payload Micro-Controller And Radio Module - A micro controller that is compatible

with Arduino and a separate radio module will be used to relay commands from the

consumer's preexisting communications to the valve controller. As was mentioned in the

Preexisting Communications section this micro-controller will have serial, I2C and digital

pins available for interface with whichever ground-to-payload communication is being

employed. This will allow the customer the flexibility to use whatever method of

communication they choose. The micro-controller will receive and information sent from

the ground and will then be able to transmit that information to the valve controller

wirelessly via its integrated radio. The wireless feature will prevent any tangling or other

complications associated with using a wired connection between the main payload and the

valve.

3. Valve Micro-Controller And Radio Module - A second microcontroller and radio module will

be used to control the valve servo using a wired PWM signal. This micro-controller and

radio module will be the same one that is used in the main payload. The Valve controller

will receive commands from the main payload via its integrated radio and then according to

the received command send a PWM signal to the servo opening or closing the valve gate.

Another one of the goals for this design is to have the ability to have the valve operate

autonomously. What is meant by this is for the valve to open and close in order to come to

neutral buoyance, or float, at a preselected altitude. In order to accomplish this the valve

controller will be interfaced to a GPS unit so that it can read altitude data. Using this altitude

data in an algorithm the controller, based on rise rates, will determine when and for how

long to open the valve in order to achieve the selected altitude.

4. Rotating Gate Valve - The method by which the Helium will be vented from the balloon will

be a rotating circular gate valve. This valve will be constructed from milled polycarbonate sheet 0.056 inch thick. The valve will consist of two circular parts that will be overlaid. The

outer and larger of the two circles will have four triangular holes placed symmetrically

about the inside of the circle, with one #6 hole at its center. This outer circle will be secured

to the end of the vent tube by a cylindrical tube cap, also milled from polycarbonate sheet.

The inside circle will be the negative of the outer ring, meaning that when the two rings are

overlaid and rotated to the correct alignment, the triangular hole in the outer ring are

closed off. This inner circle will also have a #6 hole at its center. The inner ring will have a

1/8 inch long #6 diameter pin secured to its center hole with adhesive. A four point servo

horn will be centered and secured to the opposite side with adhesive also. The servo horn

will attach to a sub-micro servo, and the servo along with a low powered compression

spring will be closed inside of the two halves of the servo casing, which will allow the

compression spring to press the servo and inner circle assembly forward, ensuring an

adequate seal between the inner and outer gate circles. The two gate circles will also be

coated with white lithium grease for lubrication, and to improve the seal made by the two

circles in contact.

5. Valve Housing - The valve housing, or main body tube, will be made from polycarbonate

tube I.D. 1 inch, wall thickness 1/16 inch. This will be cut in an 8 inch section, and have a

rectangular section removed from the lower end to allow for the servo casing to be

attached. The gate cap will then be secured, compressing the compression spring slightly.

The body tube will also have a balloon retention ring secured around the top to ensure that

the balloon will not come off during flight. The body tube will also feature an electronics

enclosure on the outside, with dimensions still to be determined.

Evaluation Criteria:

In order to make a more desirable product for the customer. A number of interviews with

potential customers were performed with the following questions.

Interview Questions

1. Our engineering team is designing a $100 microprocessor-controlled helium valve system

which will allow latex weather balloons to maintain a set, pre-selected altitude in the

atmosphere. This will allow a scientific payload to remain airborne for up to six hours.

Would your team be interested in such a product and how would the increased flight

duration be beneficial to you compared with your current flight system?

2. The helium valve being developed will be easy to attach to the industry standard Kaymont

latex weather balloons. All mechanics and electronics will be unobtrusive, light weight, and

rugged. How important is ease of use for a system such as this, and what concerns would

your team have about integrating a valve such as this into your existing flight system?

3. Our design will allow for fully autonomous operation or manual control using your existing

flight communications system (or both) to reach the desired altitude. Would your team

prefer one mode over the other?

4. Wireless communication is used to communicate between the valve assembly and the main

command and control payload. This avoids having to run external cabling which can

become tangled or damaged during flight. If wireless communication could also be extended

to your other payload electronics to facilitate wireless communication would you be

interested in such a feature? Do you have any concerns about the use of wireless

communication?

5. Are there any other features your team would like to see incorporated into this product? If

so what features?

The interviewees consisted of Berk Knighton, Randy Larimer, Angela Des Jardins, and Jen

Fowler. They provided feedback for how the product could be improved and features they would

like to see incorporated. This diverse group of potential clients includes educators, product

engineers, and field scientists. Through their unique perspectives we can determine if our plan is

converging with a perceived need that is currently underserved in the market we hope to enter.

Dr. Des Jardins' Response:

1. “I can think of several experiments that would benefit from a longer exposure to the space-

like environment as well as benefit from more time to collect data. Also, a longer flight

affords more control for landing in a preferred area.”

2. “Ease of use and reliability are certainly key. At this time, we simply tie the balloon closed

and let it burst, so adding a complicating factor would be a big step for us. If instructions

and information are very clear, I would feel more confident about using the valve. Other

concerns for integrating: we don’t have a method for cutting down our balloon – we just let

it pop. We would need some reliable way of terminating the flight at the time we wanted if

we were to have a valve. Also, we currently do basic flight predictions with an on-line

program that does not have extended flight time available. I would need help in finding out

how to predict how long to let the balloon float at what altitude, how long to vent the

balloon to get there, and in how to know when I should terminate the flight. Finally, we are

thinking about making the transition to hydrogen because it is so much less expensive. You

mention that this is a helium valve. I would want to make sure it would be okay for me to

use this valve using hydrogen as a lifting gas.”

3. “It seems to me that the only autonomous part of our current flights is that the balloon will

pop. Without that, it seems like each flight is so different, I can’t imagine how an

autonomous flight would work. That being said, in order to use manual control, I’d need lessons on how to know how much to vent and when to get my desired float time and

altitude. Also, in order to use manual control, I’d have to have some way of communicating

with the valve, right? We don’t currently have any capability for sending commands, so we’d

need that additional piece (and complication) to our set up.”

4. “Reducing tangling sounds great. We don’t currently have any communication going

between payloads (as mentioned above) – we just store the data and retrieve it – but if we

did have that capability, I could see it being useful.”

5. “I already mentioned the most important features that might be incorporated – a

termination mechanism, communication to the payloads, and flight predictions. Can’t think

of any others right now.”

Randy Larimer's Response:

1. “Yes a cost effective solution to spend more time in a radiation filled environment would be

beneficial for testing redundant computing systems. Since the cost is reasonable more

flights could be conducted compared to sounding rockets or larger NASA balloon flights.”

2. “A simple to use system would be beneficial since my team has limited ballooning

experience. Can the balloon be filled easily as helium is expensive if we mess up? Is it easy

to tell when the system is powered on and working from a distance? We do not want to

fiddle with the system.”

3. “Fully autonomous would allow my team to set the altitude and forget it, focusing on our

real time data at float altitude. I guess having a backup manual mode would be good if

things go bad during the flight. What commands and how do I send them to the valve would

be a concern. Is there a format for the commands that I must follow?”

4. “Wireless communication between multiple payloads would be great! What command

format would I use to send and receive data on this wireless link? Will the wireless link

interfere with any of my other wireless products such as GPS or iridium communication?

Will it function next to a noisy GoPro camera or other high speed devices? How many hours

of service can I expect from this wireless link? Will it last the entire time?”

5. “Some type of test feature to determine that the wireless communication is working

between payloads…LED’s or audio? Some type of addressing for multiple payloads so I

know who I am talking to? Cut down or easy fill options would be great!”

Dr. Knighton's Response:

1. “I can see some potential applications for such a device. Since we are in the business of

flying radiosondes on routine basis, several hundred a year, it seems unlikely that we would

find use in our standard application where we are simply interested in collecting vertical

profile data. Severe weather events are times when extended flight times at a specified

altitude are desirable and we would definitely find your system useful for this application. “

2. “It's got to be easy to use and robust. Even though we launch often, our group doesn't

allocate much time to the process. Because we see this as a special application we are

willing to tolerate a bit more fiddling, but we are certainly interested in a device that

interfaces well with our existing equipment.”

3. “Autonomous operation for sure. We will know ahead of time what altitude level we will

want to study. Our data retrieval system is totally automated and so not having to have a

dedicated operator is very important.”

4. “Sounds great for academic ballooning programs, but we don't have any need for

communication between our measurement payload and the valve.”

5. “Since we do not anticipate recovering the system cost is critical as is ease of use. Setting

the altitude and powering the system needs to be easy. System status lights for power, GPS

lock and altitude set point acknowledgement are important features so that we know that it

is ready to fly. The ability to be able set the altitude manually or through a smart phone

will be helpful. We don't want to have to use a computer to initialize the valve system.”

General trends in the responses of our interviewees will be covered in the Converge Plan section.

Convergence Plan:

To build a convergence plan it is important for our team to take into account the feedback

received during our interview process (with potential customers) to determine if any changes need

to be made to our final design. This ensures that we are correctly gauging the needs of the intended

market and that we are providing a product that serves to resolve a need which (we feel) is

currently lacking in this market space. Incorporating this feedback also shows that our engineering

team is aware of the importance of our client's needs which will help build loyalty between our

design team and our clients.

The response from all interviewees was generally positive on all fronts and confirms that

our product fits into a very niche market. In the following paragraphs the feedback will be

evaluated for each interview question and how that feedback will help us converge our engineering

plan towards a completed product.

The first interview question was to gauge overall interest in our overall product from

several different perspectives, including academia, meteorology, and engineering. The overall

response was positive in confirming that a device such as ours would be accepted and desired. Dr.

Des Jardins suggests that the currently available flight prediction software in this sector cannot

predict landing zones when the balloon floats/hovers during the flight. As landing prediction is a major component of traditional weather balloon flights we may need to develop our own flight

prediction software which can handle our flight profile or find products on the market which have

this capability already. Dr. Knighton indicated that he did not see a need in the market for vertical

profile radiosondes, however he noted that scientists studying extreme weather would be

interested. The potential academic clients were interested in how our product could allow for more

advanced, long duration flights for student experiments. Mr. Larimer also mentioned several

engineering specific use cases which could benefit from our system such as radiation tolerant

computing. From this feedback we note that in general our plan converges with the client's interest

in the capabilities it provides to their work. No changes would be required based on this section,

however the new areas of interest mentioned by our interviewees may indicate that we have not

fully investigated all of the potential uses for our product. It will be important for us to continue

conducting market research to find other niche applications for the helium vent.

The second interview question attempts to determine if our proposed design will be easy to

use and durable in the eyes of our potential clients. The question also opens the door for any

concerns the interviewees have about integrating the valve into their current system. The overall

response indicated that there was a slight hesitance to add additional complexity to existing

systems. Another common theme was that the system had to be as easy to use as possible to ensure

the device is actually used and to prevent errors. This does converge with several of our stated

design choices, including reducing external wiring by using wireless data transmission, integrating

a fill nozzle into the valve, and designing towards compatibility the industry standard latex balloon.

This also indicates that our team needs to potentially spend additional time on the documentation

and software design to ensure it is easy to use and configure our product. Finally, Dr. Des Jardins

inquired about our system being compatible with hydrogen gas. The industry may start to move

towards hydrogen gas as a buoyant gas since helium's price is highly dependent on oil production.

As hydrogen is explosive while helium is not this would present an additional engineering challenge and likely also change the procedures for using the valve. While we will likely not change our design

plan to accommodate hydrogen at this phase, it will be very important for us to continue to watch

the market for helium to ensure our product is viable for the future. Our team must also ensure that

sufficient warning is provided to the clients to avoid using hydrogen gas with our product.

The third question is meant to determine how involved the end user will be in the operation

and control of the valve. Our team is currently planning to have two main modes: autonomous and

fully manual. The autonomous mode attempts to reach a preselected altitude with no input from

the user other than initially inputting the altitude. Manual mode would turn off any automatic

control functions and would rely on the end user having a method to control the valve midflight,

such as another microcontroller or satellite uplink. The feedback received from our interview

sessions overwhelmingly suggests that autonomous mode will be the stand out, and preferred,

mode of operation. This suggests that we need to invest a significant portion of our development

into the code performing the autonomous decisions. We will also need to focus on very thoroughly

documenting the proper use of this mode as some clients were apprehensive about how

complicated this process may be. There was some interest in the manual control mode but mainly

for contingency reasons. A standard protocol document which explains how the end user will

interface with and control the valve in manual mode will need to be thorough in scope. The

feedback received from these interviews suggests that our current engineering plan will converge

with the needs of our clients.

The fourth question asked of our interview panel was used to determine if the wireless

communication that we plan to implement would be a useful feature to the clients. Specifically we

currently plan to use wireless communication between the valve mechanism and the main control

system microcomputer which resides in a command payload below the valve (approximately 20

feet away). An additional feature our engineering team is planning on implementing is a general wireless communication spec which would allow the clients to send data between payloads. This

would rely on wireless expansion modules that we would package in with our product. The

majority of those interviewed felt the wireless communication with the valve is a great idea that

they would like to see implemented. The wireless expansion modules sparked interest for those in

academic settings. As with most of our features, the interviewees wanted to know exactly how

these modules would work and how they would implement them into their current systems. This

suggests again (as a common theme) that we must have very thorough documentation which

describes the details required for using these more advanced features. Dr. Knighton suggests that

the radiosonde community would not see as much value in wireless communication. Our team will

need to determine if this suggests we need to explain the virtues of the wireless capabilities with

these groups more thoroughly, or if we need to market the other features of the valve to this

specific market (radiosonde meteorological community). The feedback received suggests that our

current engineering plan for this feature will converge with the requirements of our academia

clients, and our overall system will still be beneficial to the meteorological community.

The fifth and final question was open ended in an attempt to gather any other general

feedback the potential clients had to offer. The common themes mentioned were ease of use,

confirmation of proper operation, and low cost. Ease of use has been a common theme throughout

our interviews which again suggests our documentation needs to be thorough. The overall system

must also have features to indicate proper operation and status. LED status indicators were

mentioned several times as a way to confirm operation. This was not previously something the

engineering team considered so we must implement this feature to converge our plan with our

client’s needs. Dr. Knighton mentioned cost as a main metric by which our system would be

evaluated to the meteorological community. Referencing his suggestions to question four, this may

suggest that a second model of our valve could be developed with cost as main design factor.

Removing extra features such as wireless communication may result in an inexpensive product which is more desirable to that community. If we implement these suggested features our plan will

converge on a product which our clients would be interested in using.

Contingency Plan:

There is some chance that our design choices will not work. In order to minimize the impact

on the end product it is necessary to make a contingency plan. Two potentially problematic design

choices are the valve design (it may not allow for the necessary amount of air flow), and the

selected microcontroller configuration (it might not interface as well as we would like or it might

consume too much power during operation).

If the microcontroller configuration selected does not work for various reasons the

contingency plan is to use the next design alternative that scored the next highest in the decision

matrix. If it is required we could select a low power, less powerful micro-controller for our design.

Also a more commonly used microcontroller could be selected, one that has been previously used

with a radio module for something similar to this application and has example code available.

There is a question as to whether or not the gate valve will have a high enough flow rate to

provide the user with neutral buoyancy within the specified vent time window. The gate valve

currently utilizes approximately 45% of the flow area available within the geometry of the flow

tube. If the flow rate ends up being inadequate, the butterfly style valve will be used. This valve will

allow an estimated 75% of the effective flow area provided by the inner geometry of the flow tube.

System Architecture

Introduction:

This Report will detail the system Architecture for the Weather Balloon Altitude Control

Project. The report will first explain in detail the system architecture plan for the project, covering

the major interfaces, their position in the assembly, and their function. This includes The flow tube,

the gate valve, the nozzle of the balloon, the main payload microcontroller, and the valve servo. This

section will be divided into mechanical and electrical groups to clarify the nature of each system

and its respective interfaces. The next section will cover the system interfaces together in a block

diagram. This representation will provide better insight into the different sections, and how they

interface. The next section will detail the sub-system interfaces. This includes the valve controller,

any third party communication payload, and the commands uploaded by the user during flight. For

this project, these are entirely electrical, and are explained below in more detail. Finally, the report

will cover the user interface for this project. this will include any setup, handling or operational

interfaces the user may encounter while using this system. For this project, user interface includes

attaching the balloon to the valve, filling the balloon through the valve using the fill station,

attaching the payload to the bottom of the valve, programming the microcontroller, and interfacing

the user's existing communications payload to the valve controller.

System Architecture Plan:

Mechanical:

The mechanical portion of the valve project will have 3 interface connections. The first will

be an interface with the Helium fill station nozzle. This nozzle, when connected, will press a limit

switch connected to the microcontroller. this controller, after reading the switch as being pressed,

will activate the servo, and open the gate of the valve. this will allow for Helium to pass through the tube of the valve into the balloon, which is the second interface. The flow tube of the valve has been

sized such that the nozzle of the balloon will fit over it snugly. The retention ring ( a raised portion

on the balloon end of the valve tube) causes the latex of the balloon nozzle to stretch, ensuring a gas

tight seal between the valve and the balloon nozzle. The third interface on the valve project is the

interface between the servo and the microcontroller. This allows the microcontroller to open or

close the valve when its logic is instructed to do so.

- Interface between the bottom of the valve and the Helium fill nozzle
- Interface between the top of the valve and the balloon nozzle
- Interface between the valve gate servo motor and the microcontroller

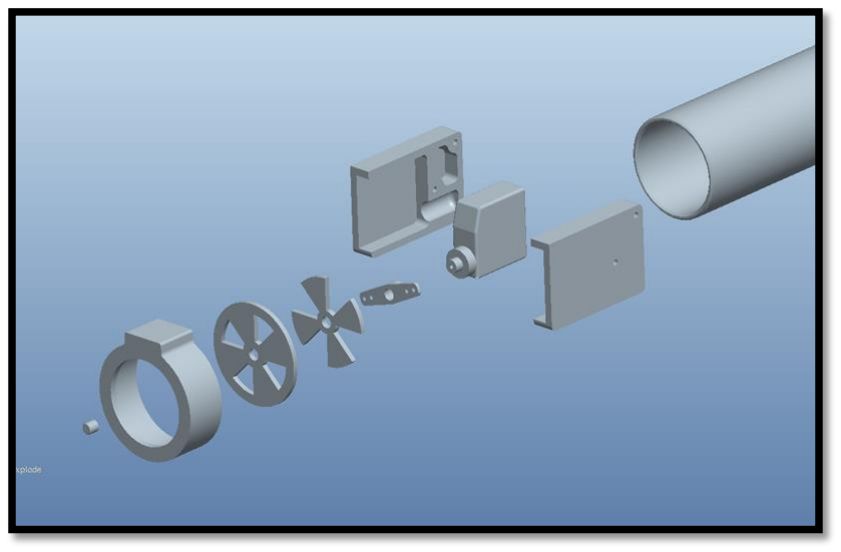
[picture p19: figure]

Figure 1: Exploded CAD model of the Valve geometry

Electrical:

The electrical portion of this project will consists of interfaces between electrical

components, mechanical components, and the user. The first interface will be the interface between

the customers communications system and the microcontroller in the main payload. This is

interface will have user selectable options: serial, I2C, and or some digital control lines. The user will be able to send commands and receive data via these this interface. The next interface is the

interface between the main payload micro-controller and the micro-controller on the valve. This

interface is going to be a wireless connection. This is achieved with a radio module controlled by a

micro-controller. Next the valve microcontroller interfaces to the servo that controls the valve gate

with a pulse width modulated signal. The user will interface with the microcontrollers by

connecting the microcontroller to a computer via USB cable and uploading their desired code.

- Interface between the user's communication system and the main payload micro-controller
- Interface between the main pay load and the valve micro-controller
- Interface between valve micro-controller and the valve servo
- Interface between the user and the microcontrollers

System Interfaces:

The following figure shows the different components of the system and how they interface

together.

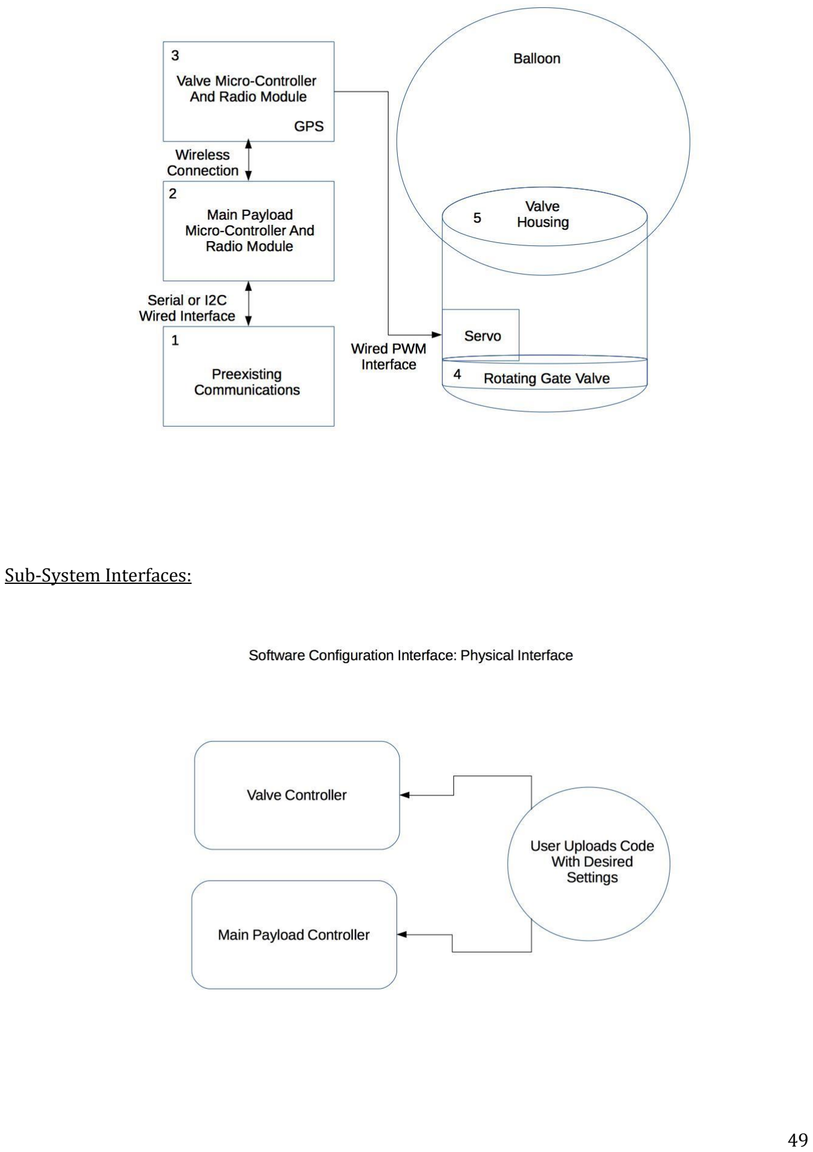
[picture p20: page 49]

Sub-System Interfaces:

Software configuration interface: physical interface - The physical interface of the software

configuration interface describes the electrical connection of the programming cable with the main

payload controller. The user must plug a USB cable into their computer and connect the other end

with the main payload microcontroller, and then with the valve microcontroller. A label or graphic

will guide the user to the correct location for the programming cable. Then the settings outlined in

the user manual will be changed by the user according to their preference.

Software configuration interface: software interface - The software configuration interface is used

to program the main payload and valve controllers with the settings selected by the user. This

interface consists of a graphical user interface running on the customer-provided computer and any

setup or installation required to get the software running. The user must interact with the software

to select their desired settings.

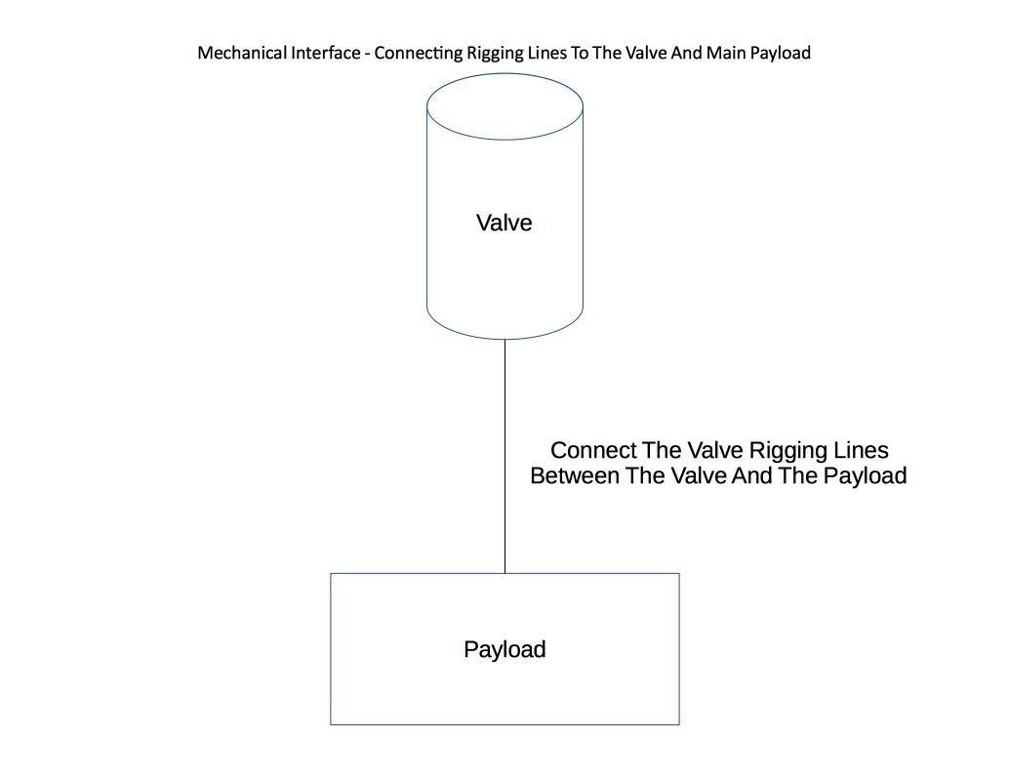
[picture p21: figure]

Mechanical interface: connecting rigging lines to the valve and main payload - The mechanical

interface between the valve and main payload requires the user to physically couple their payload

to the helium valve hardware. The rigging lines used will be provided by the customer however our

product will provide hard mounting points to securely attach these lines to the valve.

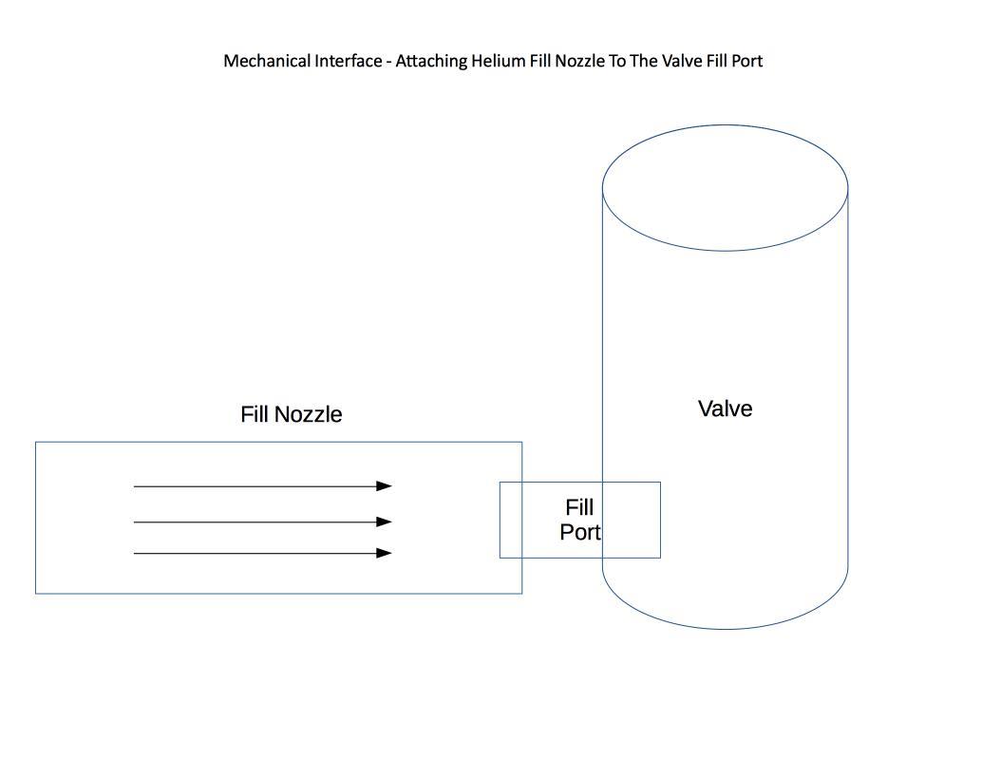
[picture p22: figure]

Mechanical interface: attaching helium fill nozzle to the valve fill port - The mechanical interface

between the fill nozzle and fill port requires the user to physically connect a fill nozzle from their

helium tank and regulator to the fill port of the valve assembly. The user must then operate their

helium filling equipment to fill the latex weather balloon as needed.

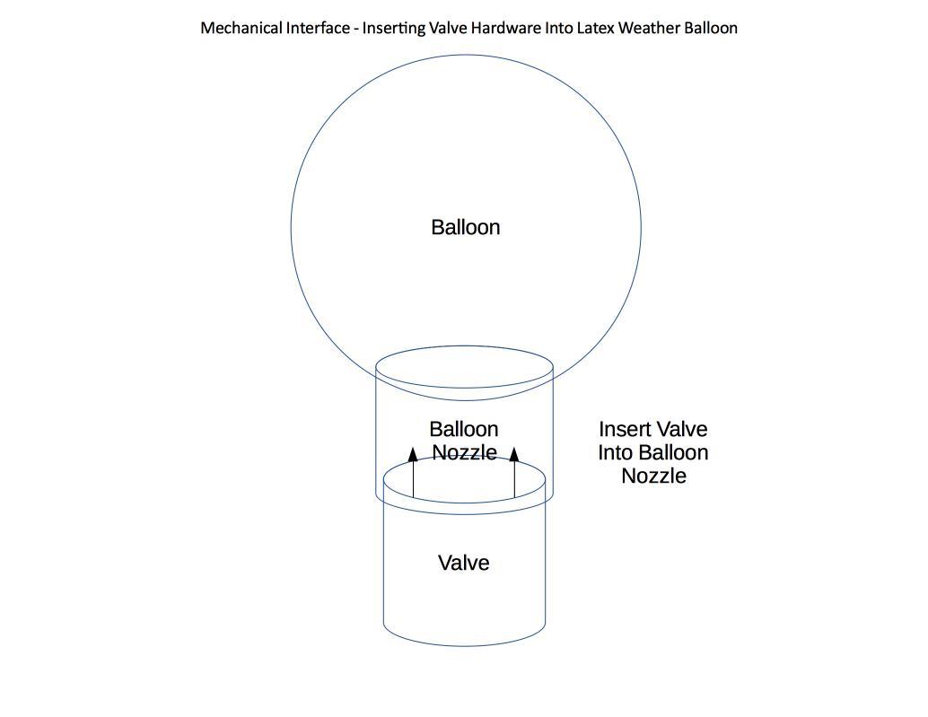
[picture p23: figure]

Mechanical interface: inserting valve hardware into latex weather balloon - The mechanical

interface between the customer's latex weather balloon and the valve assembly requires the user to

mechanically insert the valve sub-assembly into the balloon nozzle. Once the valve has been

inserted to a reference mark the customer must secure the valve to the balloon using zip-ties or

other similar means.

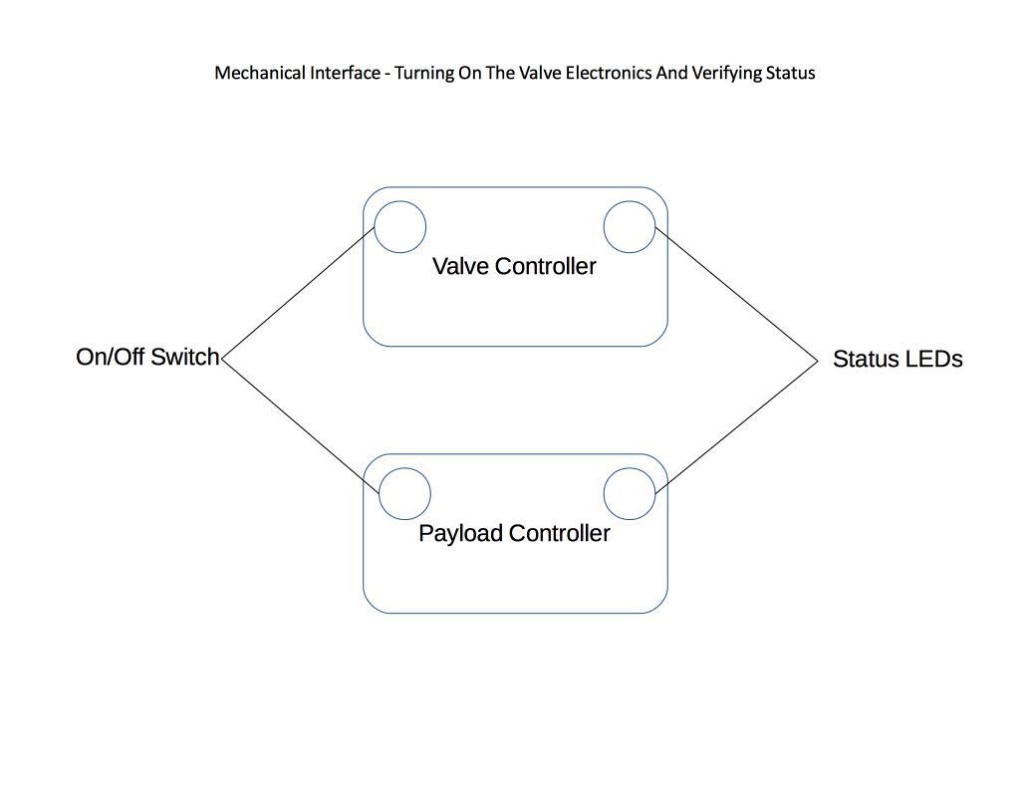
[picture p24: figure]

Mechanical interface: turning on the valve electronics and verifying status - The valve electronics

require a mechanical interface between the user and the product activation switches. The user must

physically actuate the power switch to turn on the valve electronics. Once the electronics have

powered up the user must verify proper operation using status LEDs located on the valve

hardware.

User Interfaces:

The user interfaces for the balloon valve system consist of two main components: the

mechanical assembly and construction of the valve with the balloon, and the electrical connections

and configurations required to operate and program the system. This section will describe the

human factors required for proper operation of both components. This will include any part of the

valve system which a human must touch or interact with to properly operation our product.

The first main component of the user interface will be those related to the mechanical and

physical valve assemblies. First the valve housing assembly user interface will be detailed (which

connects to the latex weather balloon), then the main payload subsystem interface (which is used to

interface with the customer's tracking system) will be detailed.

The valve housing assembly will likely have the most human contact over all other systems

in our product. The valve housing assembly has three main sub-interfaces: connection of the latex

weather balloon to the valve, attaching or detaching the helium fill nozzle, and turning the system

on and verifying operation.

Attaching the latex weather balloon will be a critical step requiring the user to physically

insert the valve into the balloon nozzle. As we are designing the valve hardware to fit within a

standard Kaymont weather balloon this operation should not require heavy exertion by the user.

The user must hold the latex weather balloon nozzle in one hand, and guide the valve assembly into

the balloon nozzle with the other hand. Once the valve is inserted far enough into the latex balloon

(indicated by a reference mark) they will need to secure the balloon to the valve using zip-ties to

ensure the balloon does not slip off during use. The user must then physically couple their main

payload to the valve using their own rigging materials. The valve will provide hard mounting points

which the user may use to affix nylon rope (or similar) as required.

The second mechanical interface will be between the helium fill nozzle and the valve (which has

already been inserted into the latex balloon). This consists of attaching a helium fill tank (which the

user must supply and know how to operate) to the valve such that the balloon may be inflated. As

the valve itself starts in the closed position the user will be able to fill the latex balloon with the

valve assembly already assembled. Our product will supply a fill nozzle or adapter which will

connect to the customer's helium tank using industry standard hardware. The user must physically

couple the helium fill tube (connected to their helium tank and regulator) to the valve assembly and ensure it is connected securely before turning on the helium flow through the regulator. Once the

balloon has been filled to customer specifications the user will then need to decouple the helium fill

tube from the valve assembly.

The third and final mechanical interface will be turning on the system and verifying it is

operational. Both the main payload controller and the valve assembly will have electronics which

must be activated prior to use. The product will have a switch or other method used to turn on each

device and status LEDs which indicate proper operation. Activating the system will require that the

user manipulates the activation mechanism and also observes the status LEDs which appear.

The electrical connections and software configurations are the other primary interface with

our product. These components will be used to configure the microcontroller for proper operation

and ensure the customer's systems can properly communicate data with our product.

The electrical connection is the physical coupling of the main payload controller with the

client's tracking and communication system. The main payload controller will contain data ports or

screw terminals which the user must electrically connect to their system (if this functionality is to

be used by the client). This may involve the user providing their own cables and tools (such as

screwdrivers) to mechanically couple these devices. A protocol datasheet will be provided with the

product which will describe how the user must communicate (through their tracking and

communication system) with our product. The user must be able to interpret this protocol and

configure their own equipment as needed for this data link.

The second electrical and configuration user interface will be the software graphical user

interface used to configure the product to the user's requirements, in this case the Arduino

programming IDE and the Xbee configuration software, XCTU. This software must be executed on

the user's computer by downloading it from a location we specify. The software will provide

meaningful labels or instructions guiding them through the process of configuring the valve electronics. The user will select or enter various settings into the software according to their needs,

such as manual or autonomous mode and the desired float altitude. Once all settings have been

entered the user will connect a USB cable to their computer (which is provided with the valve

system) and the other end of the cable into the main payload controller. This will start the software

programming of the user selected configurations onto the microcontroller of the main payload

controller. Labels or other indicators will be present on the main payload controller which will help

the user select the correct port to plug the programming cable into. A graphical alert will instruct

the user when the programming process is complete, after which they may unplug the

programming cable. Status LEDs will provide some low level indication of configuration and

operating status.

Detailed Design

Introduction:

This section outlines the materials required for this design and their specifications. This

product can be divided into two sections, the mechanical or valve section and the electrical or

controller section. The valve section will require numerous custom and off the shelf pieces of

hardware to produce. The electrical section requires microcontrollers, a GPS unit, various circuit

elements, and two custom made printed circuit boards. There are some possible production issues

that need to be kept in mind when designing and getting ready to produce this product, such as a

shortage of the items required to build this product. A potential customer will want to know how

the product will perform and what its expected lifetime is, for instance the fact that this product is

designed to for one use, but could potentially last much longer should the consumer choose to

retrieve and reuse it.

Layout Drawings:

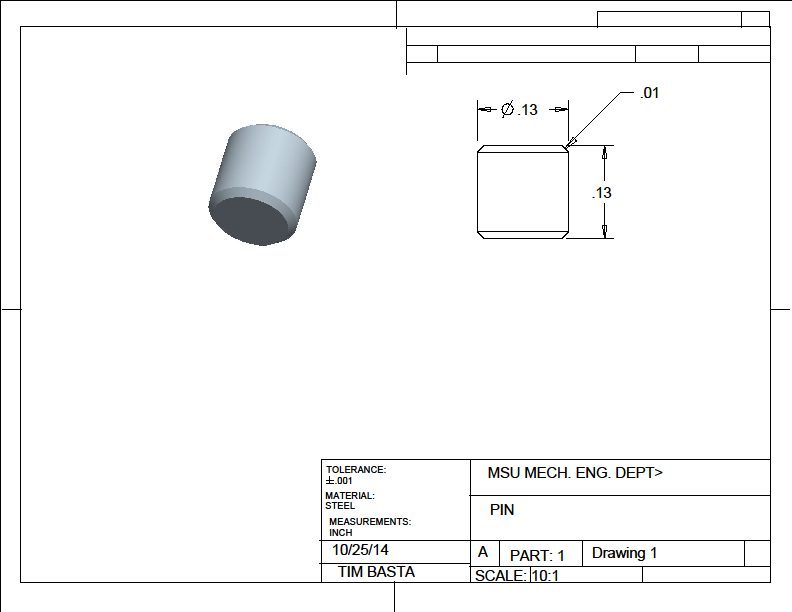
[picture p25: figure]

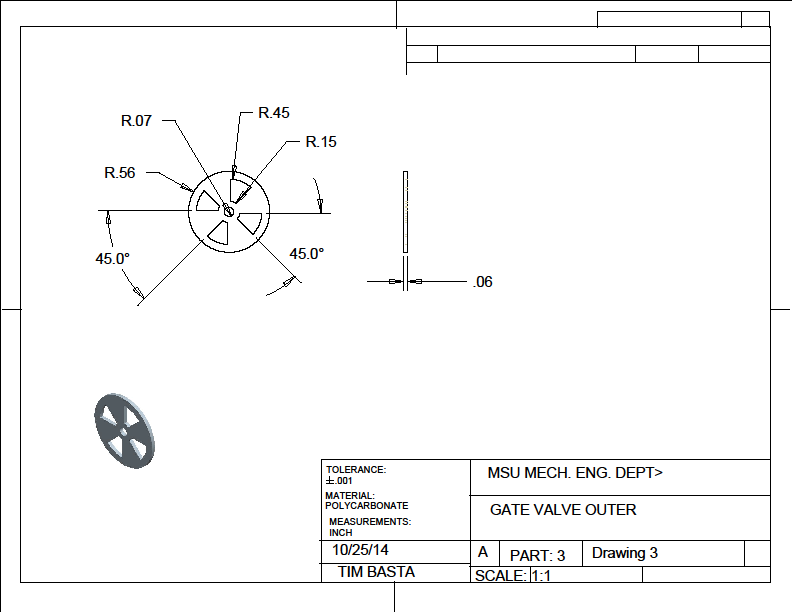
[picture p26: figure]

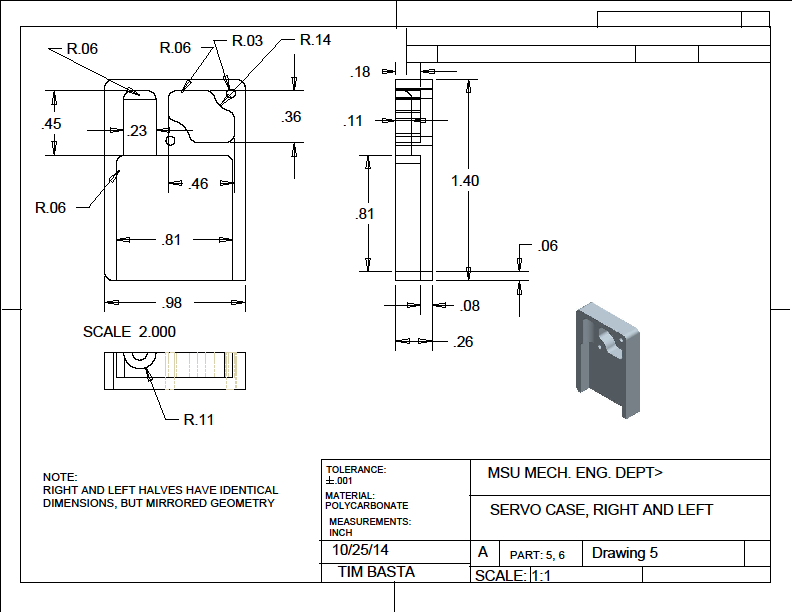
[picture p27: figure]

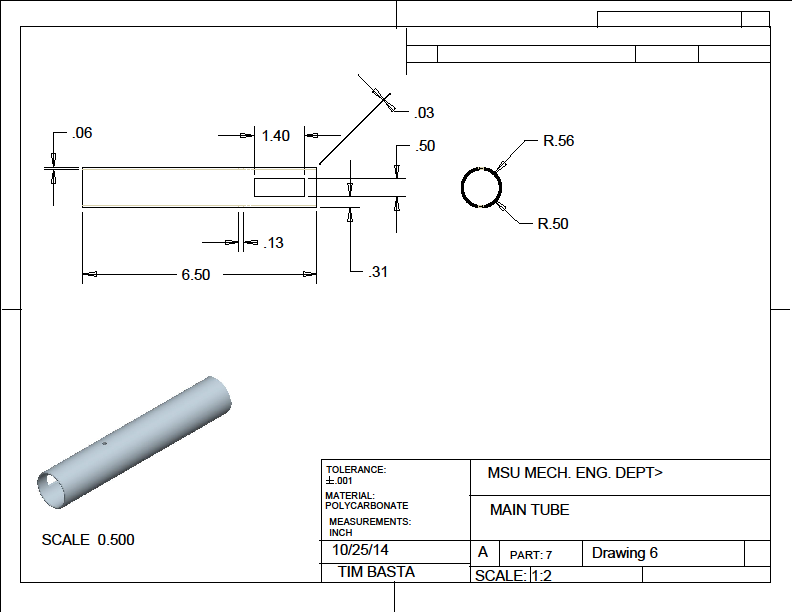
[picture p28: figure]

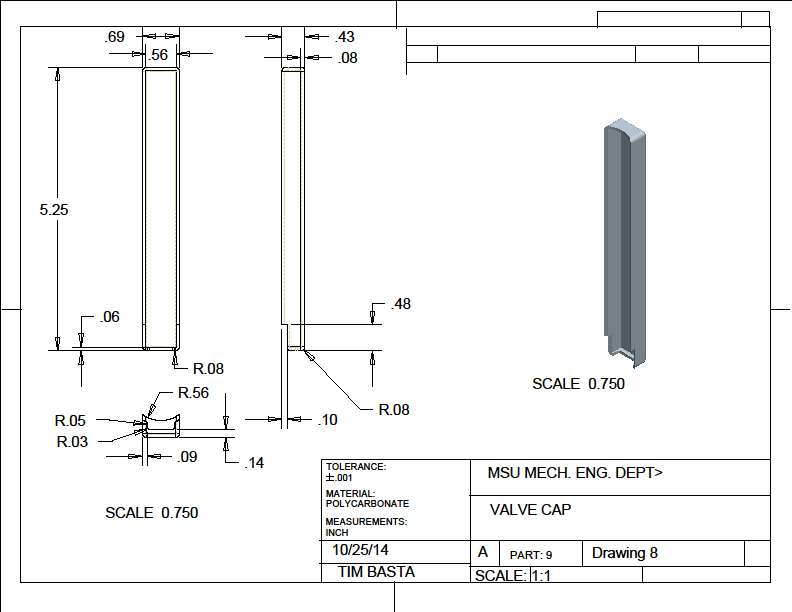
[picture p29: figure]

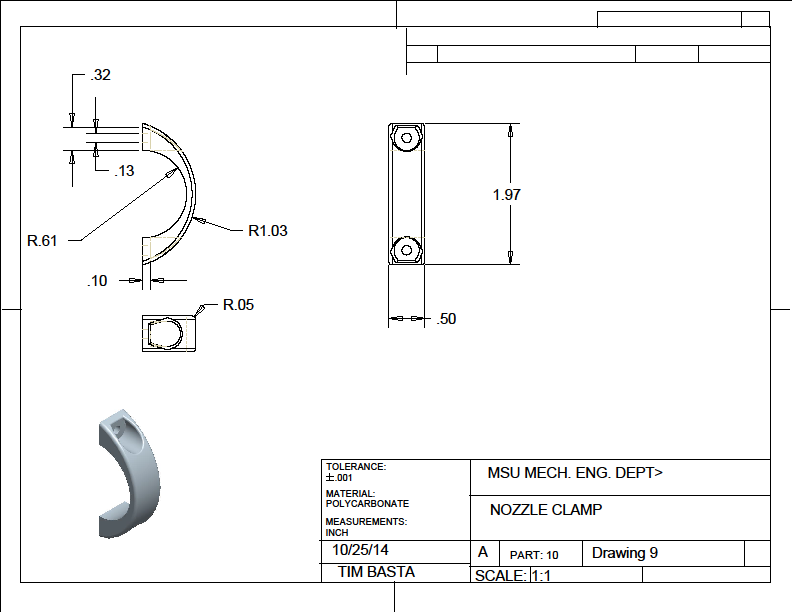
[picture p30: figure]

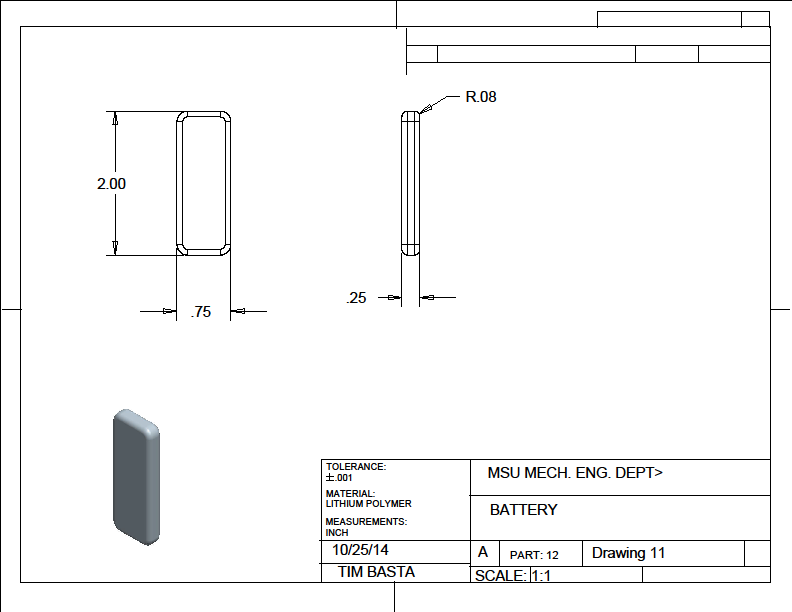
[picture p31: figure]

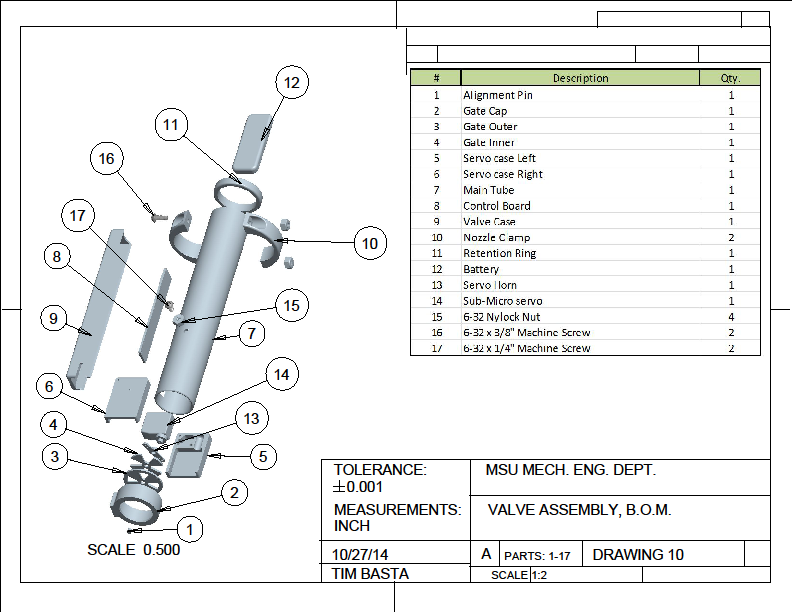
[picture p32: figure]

Bill of Materials

# | Description | Qty.

1 | Alginment Pin | 1
2 | Gate Cap | 1
3 | Gate Outer | 1
4 | Gate Inner | 1
5 | Servo Case Left | 1
6 | Servo Case Right | 1
7 | Main Tube | 1
8 | Control Board | 1
9 | Valve Case | 1
10 | Nozzle Clamp | 2
11 | Retention Ring | 1
12 | Battery | 1
13 | Servo Horn | 1
14 | Sub-Micro Servo | 1
15 | 6-32 Nylock Nut | 4
16 | 6-32 x 3/8" Machine Screw | 2
17 | 6-32 x 1/4" Machine Screw | 2
18 | Main Payload Micro-Controller (ATmega328) | 1
19 | Valve Micro-Controller (ATmega328) | 1
20 | GPS MTK3339 | 1

21 | Miscellaneous discrete electronics parts (to be determined) | NA
22 | Xbee Radio Modules (XB24CZ7RIS-004) | 2

Purchased Component Specifications

# | Description | Qty.

13 | Servo Horn | 1
14 | Sub-Micro servo | 1
15 | 6-32 Nylock Nut | 4
16 | 6-32 x 3/8" Machine Screw | 2
17 | 6-32 x 1/4" Machine Screw | 2
18/19 | Micro-Controller - ATmega328 | 2
20 | GPS Unit - MTK3339 | 1
21 | Electronic Components TBD | NA

Specifications -

GPS Unit - MTK3339

- -165 dBm sensitivity, 10 Hz updates, 66 channels
- Ultra low power usage: 20mA current draw while tracking
- 3.3V operation,
- RTC battery-compatible
- Built-in datalogging
- PPS output on fix
- We have received reports that it works up to ~32Km altitude (the GPS theoretically does not have a limit until 40Km)
- Internal patch antenna + connection for optional external active antenna
- Fix status output
- Ultra small size: only 16mm x 16mm x 5mm and 4 grams

Micro-Controller -ATmega328

- 16 MHz
- Arduino compatible
- I2C
- SPI
- UART

Xbee Radio Modules (XB24CZ7RIS-004)

- 60m Indoor/Urban Range
- 1200m Outdoor/RF Line-of-Sight Range
- Transmit Power - 3.1 mW (+5 dBm) / 6.3 mW (+8 dBm) boost mode
- Receiver Sensitivity (1% PER) - 100 dBm / -102 dBm boost mode
- Data Rate - RF 250 Kbps, Serial up to 1 Mbps
- Configuration Method - API or AT commands, local or over-the-air
- Serial Data Interface - UART, SPI
- Frequency Band - ISM 2.4 GHz
- Dimensions (L x W) and Weight - 0.87 in x 1.33 in x 0.12 in (2.20 cm x 3.40 cm x 0.30 cm);

1.40 oz (40.00g)

Printed Circuit Boards

- Two Printed Circuit Boards:
- One to accommodate the main payload controller
- One to accommodate the valve controller and a GPS unit

- Designed with a minimal footprint
- F Antennas for the IEEE 802.15.4 radios will be designed into the printed circuit board

Detailed Design:

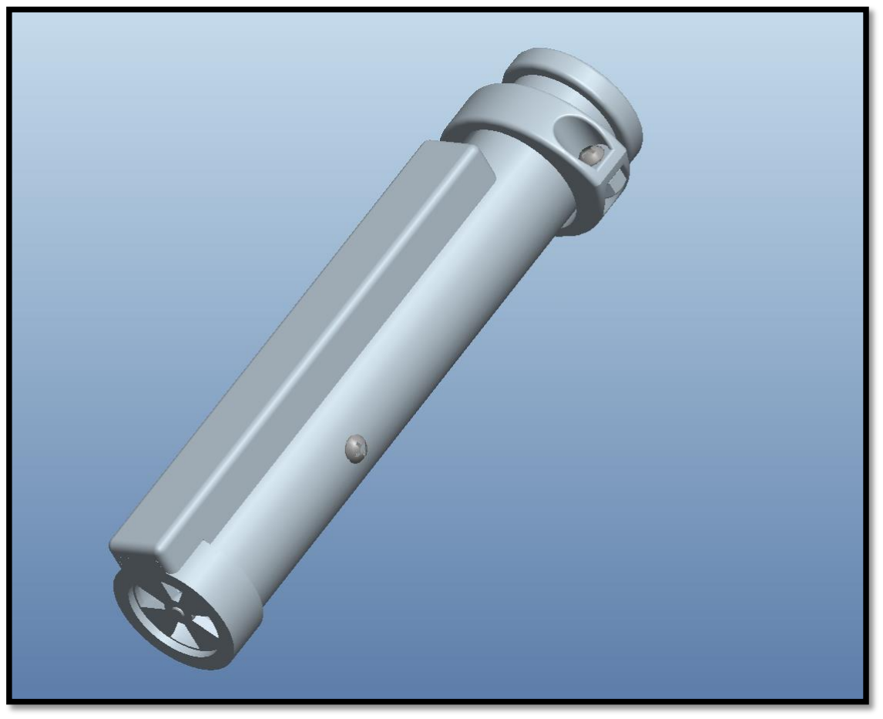
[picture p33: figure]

Valve Assembly, 10/27/14

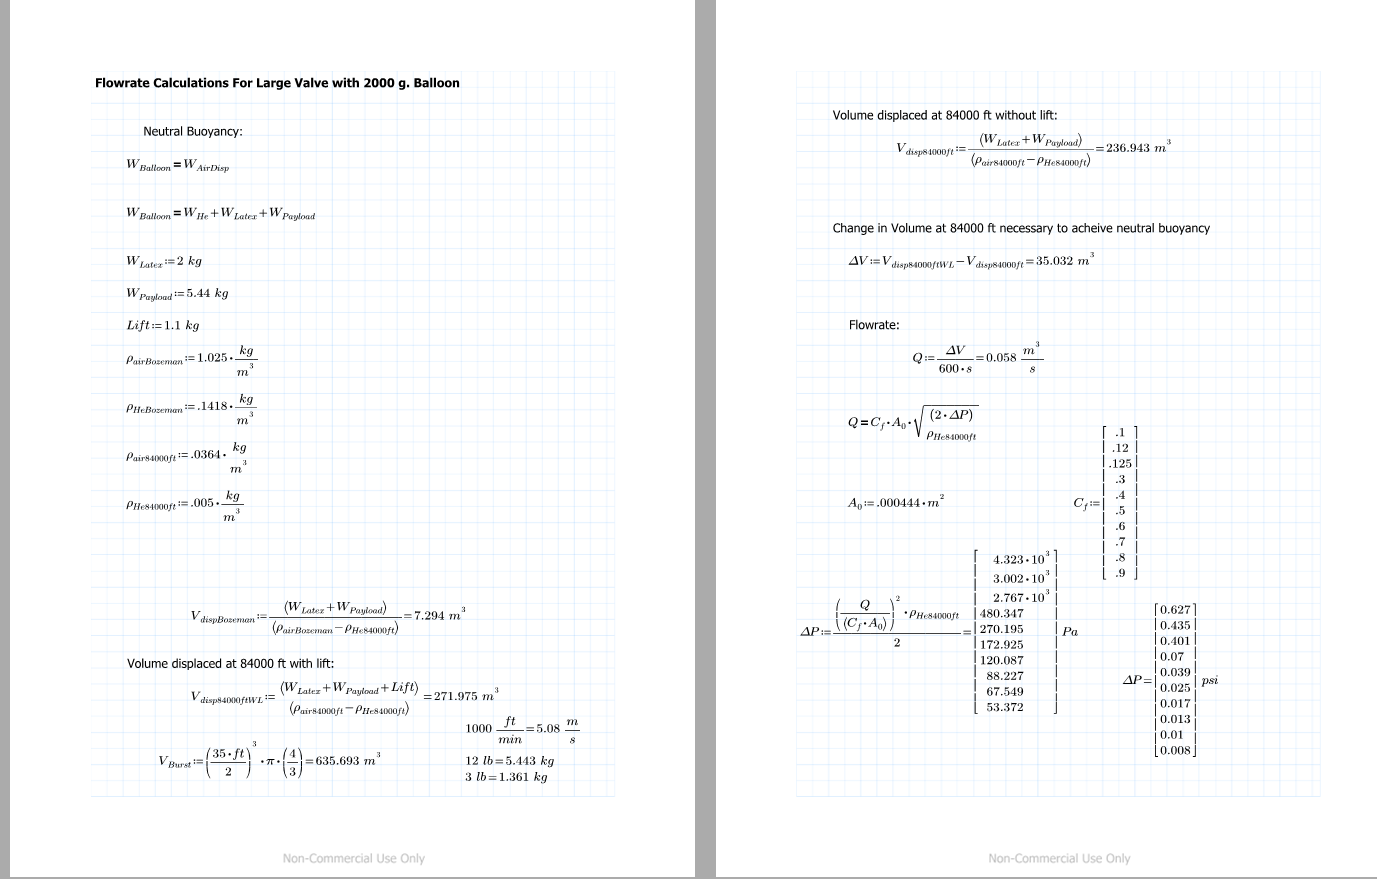
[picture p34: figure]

Valve Flow-rate Calculations. Note: Final flow-Rate for Valve will be calculated pending results of

flow-rate experiment.

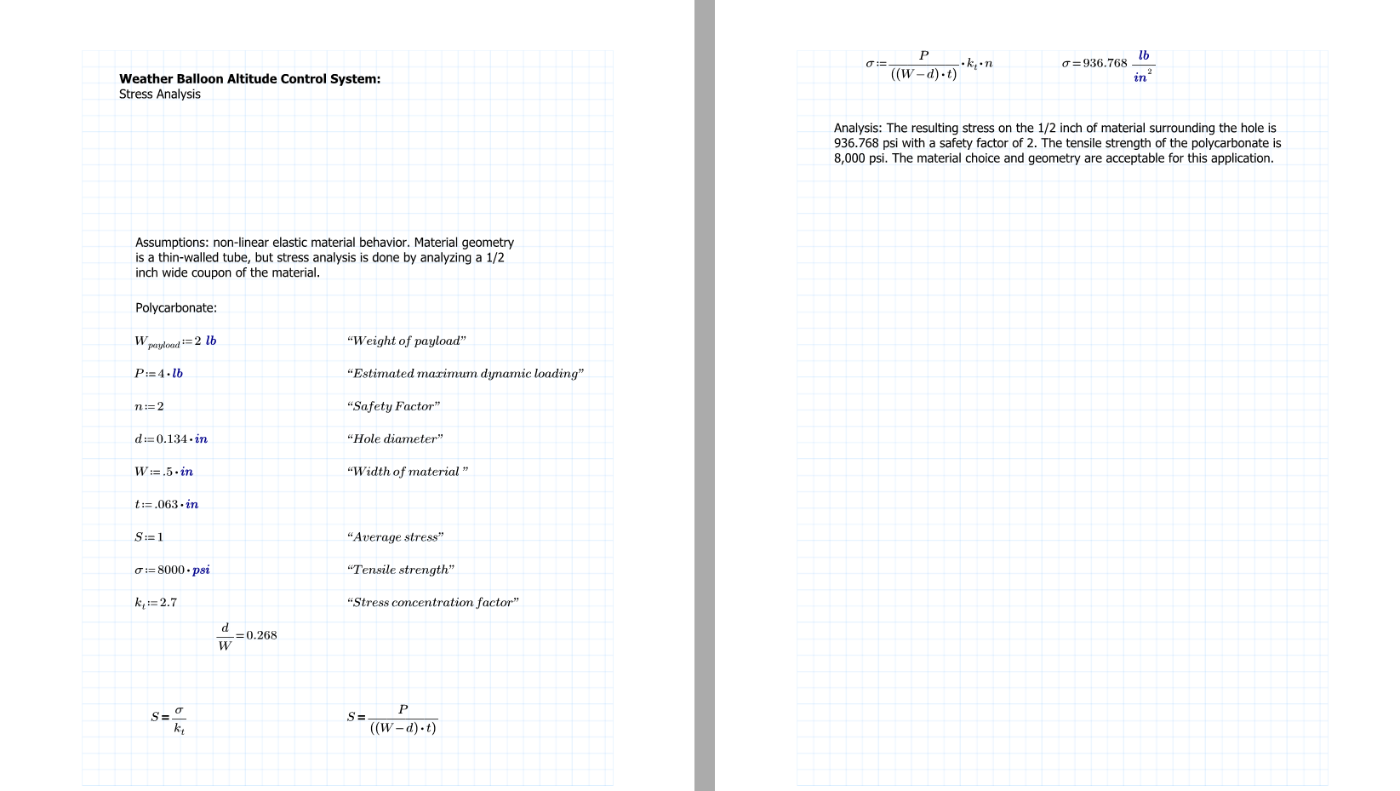
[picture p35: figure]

Valve Mechanical calculations

Micro Controller Interface and Wireless Communications:

The two microcontrollers, one in the main payload and one on the valve, will communicate

via a 2.4 Ghz radio module using the Zigbee protocol. These radios are designed for short range

communications.. The typical distance that these microcontrollers will need to communicate over

will be approximately 4 meters. These radios should be more than capable to transmit and receive

over this distance. The interface between the main payload microcontroller and the consumer’s

preexisting communications system can be I2C, UART, or some digital control lines.

Product Lifecycle :

This product is designed to be a single use item, much like traditional radio sondes. The product

will be something the consumer has to buy prior to each flight. Unfortunately due to the nature of

ballooning once the balloon is launched it is generally not recovered so recycling is not applicable

and the final disposal of the product is it being left out in the environment. Most components

utilized in the design are inert or non-toxic which should prevent environmental contamination.

Should the consumer choose to recover the product it will be reusable. The lifetime of the product

should the consumer choose to recover it could potentially be tens of uses. To reuse the product all

the consumer would have to do is recharge or replace the battery and if necessary upload new

software to the microcontrollers.

Production issues could cause delays in the shipment of the product to our clients. Most of the parts

produced for the valve system will require machining of raw materials for the physical construction

of the valve. Any delay in acquiring these raw materials could cause the production to slow or stop

especially if an outside machining service is used. That being stated none of the raw materials are

exotic and are easily procured locally or through a supplier. The main printed circuit boards will

not be manufactured in-house and as such will be vulnerable to any production delays at the

manufacturer. The discrete components used to populate the printed circuit board are not exotic

and it is not expected that a shortage or delay would be incurred in ordering them. Several major

component suppliers (DigiKey, Jameco, etc) can supply these components in abundance.

From production to the end of the life of the product the timespan will probably be a couple of

months at a minimum and if the consumer reuses the product it could be as long as a couple years.

This really depends on the consumer and how they choose to use the product.

Analysis and Test

Introduction:

Failure Modes and Effects Analysis:

Potential Failure | Effect | Prevention
Balloon disconnects from Valve assembly | Premature descent of the payload, Potential to lose payload. | Locking clamp assembly on the neck of the valve
Valve Fails to vent adequate Helium | Premature descent of the payload, Potential to lose payload. | Ground testing and design to ensure adequate flow rate
Mechanical Failure | Premature descent of the payload, Potential to lose payload. | Mechanical components designed with an appropriate safety factor
Balloon reaches neutral buoyancy and passes out of control range | Loss of payload | independent timer failsafe that will open the vent after the mission clock has expired
Communications Failure | loss of control, and potential loss of payload. | Extensive testing to make sure that under normal operating conditions the communications link will be on.
Autonomous Valve Algorithm Failure | potential loss of payload. | Extensive testing and simulation.
Code failure | loss of control, and potential loss of payload. | Extensive testing and simulation.
General Electronics Failure | loss of control, and potential loss of payload. | Testing of electronic components to make sure they are working properly.

Physical Testing:

A flow rate test for the vent gate of the valve will be conducted as soon as possible. This will

be a physical test of the mechanics of the system to determine their effectiveness at ambient

conditions. this test will also provide a value for the flow coefficient used in the flow rate

calculations, which is currently unknown. This test will also provide a mechanical tension test of the

valve structure, as it will be stressed in the same way as it will be in actual operation.

While preparing for the critical subsystem demo it was discovered that the selected design

for the microcontrollers and the 2.4 GHz was not going to work for this application as well as had

been expected. It was going to be far too complicated for customers and students who didn't have a

lot of experience with programming to configure and customize the product to their specific

application. This caused a reevaluation of the decision matrix to rescore the ease of use design

metric. This resulted in changing designs from the micro-controller with a build in radio to an

Arduino compatible microcontroller and a separate radio module. This will be much simpler for the

user to customize and configure the product.

Cost Analysis:

Component | Qty. | Raw Matl. Cost (per 100) | Fabrication Cost | Assembly Cost | Testing Cost
Alignment Pin | 1 | 0.03 | 0 | 0 | 0
Gate Cap | 1 | 0.80 | 0 | 0 | 0
Gate Outer | 1 | 0.05 | 0 | 0 | 0
Gate Inner | 1 | 0.05 | 0 | 0 | 0
Servo Case Left | 1 | 0.80 | 0 | 0 | 0
Servo Case Right | 1 | 0.80 | 0 | 0 | 0
Main Tube | 1 | 3.14 | 0 | 0 | 0

Valve Case | 1 | 2.00 | 0 | 0 | 0
Nozzle clamp | 2 | .80 | 0 | 0 | 0
Retention Ring | 1 | 1.60 | 0 | 0 | 0
Battery | 1 | 10.00 | 0 | 0 | 0
Sub -Micro Servo | 1 | 8.00 | 0 | 0 | 0
6 -32 Nylock Nut | 4 | 0.04 | 0 | 0 | 0
6 -32x3/8" Mach. Screw | 2 | 0.10 | 0 | 0 | 0
6 -32x1/4" Mach. Screw | 2 | 0.10 | 0 | 0 | 0
GPS MTK3339 | 1 | 16.33 | 0 | 0 | 0
Xbee Radio Modules (XB24CZ7RIS -004) | 2 | 22.85 | 0 | | 0
Micro Controller (ATmega328) | 2 | 5.20 | 0 | 0 | 0
PCB | 2 | 20 | 0 | 0 | 0
Misc. Electronic Components | ~ | ~5 | 0 | 0 | 0

Total Valve
Assembly

97.69

0

0 | $300/ Test

Once a working prototype has been fabricated and numerous tests and simulations have

been done test flights on actual balloons will have to be conducted. Currently there are 3 test flights

and then one final demonstration flight allotted for this project. Each flight will cost approximately

$300. These flights are critical in making sure everything operates as intended.

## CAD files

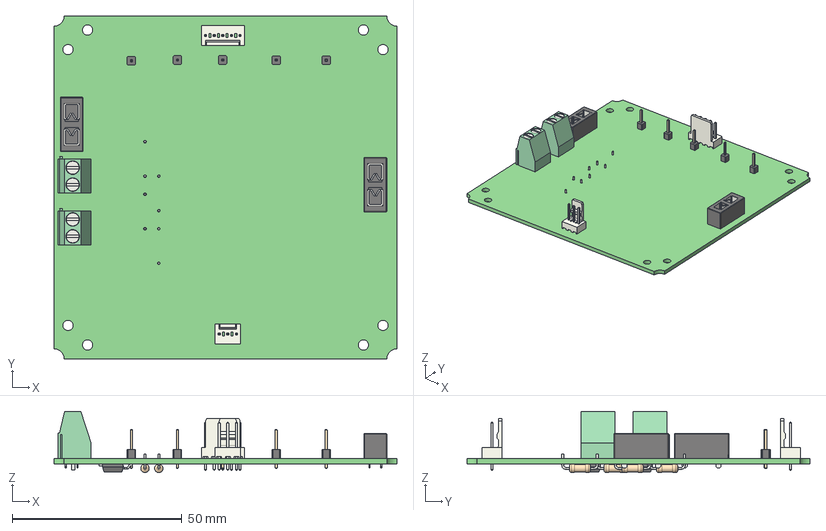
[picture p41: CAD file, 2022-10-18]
HW-Kicad/batteryboard/batteryboard.step
101.0 x 101.0 x 18.0 mm
batteryboard PCB

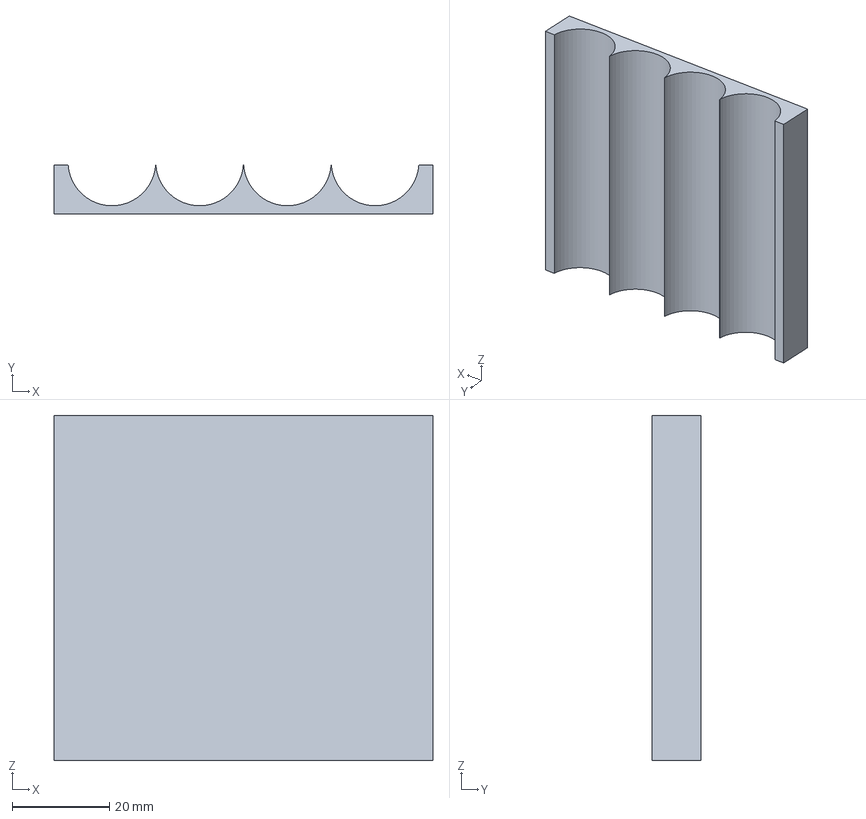
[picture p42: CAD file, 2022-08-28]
HW-Kicad/batteryboard/Components/holderBaterias.step
77.8 x 10.0 x 70.8 mm

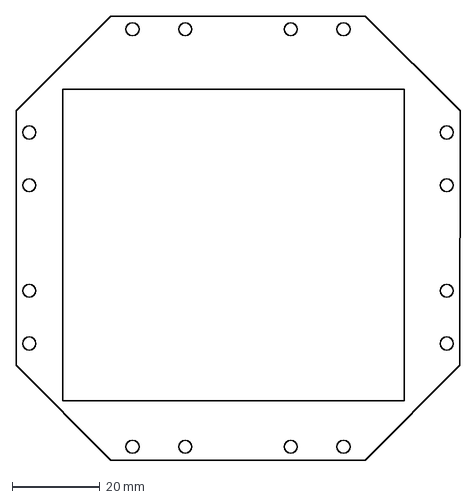
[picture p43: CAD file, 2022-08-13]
HW-Kicad/batteryboard/Components/LM2596/base_bateryholder.dxf
101.0 x 101.0 mm

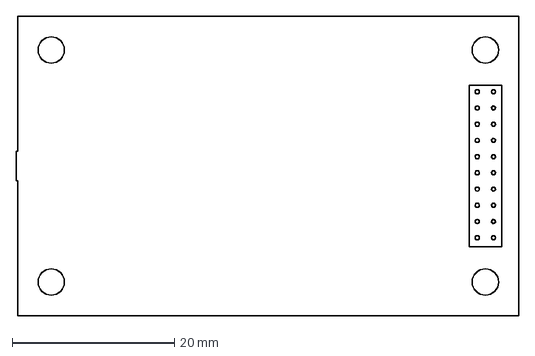
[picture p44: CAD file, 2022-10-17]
HW-Kicad/mainboard1/Components/9xtend/xbee_footprint.dxf
62.0 x 36.9 mm

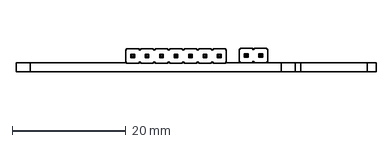
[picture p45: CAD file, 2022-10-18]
HW-Kicad/mainboard1/Components/LightAPRS/footprintaprs.dxf
63.4 x 4.14 mm

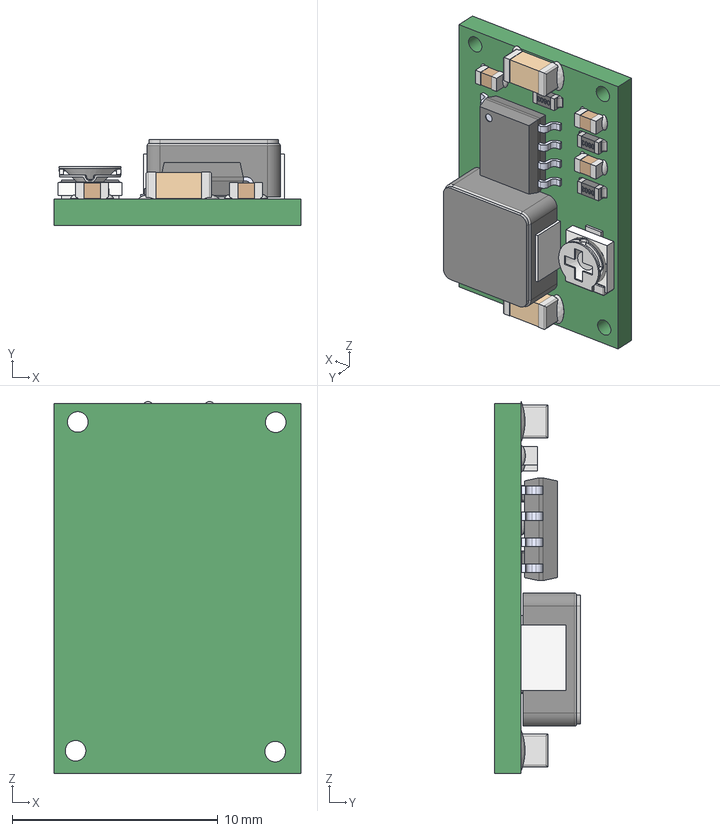
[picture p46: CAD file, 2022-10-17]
HW-Kicad/mainboard1/Components/Mini360_step_down_converter/mini360.step
12.0 x 4.20 x 18.1 mm
User Library-SOIC-8 - TEK
Resistor 0603 x 3
CAPC0603 x 3
CAPC1206 x 2
EVM-3E

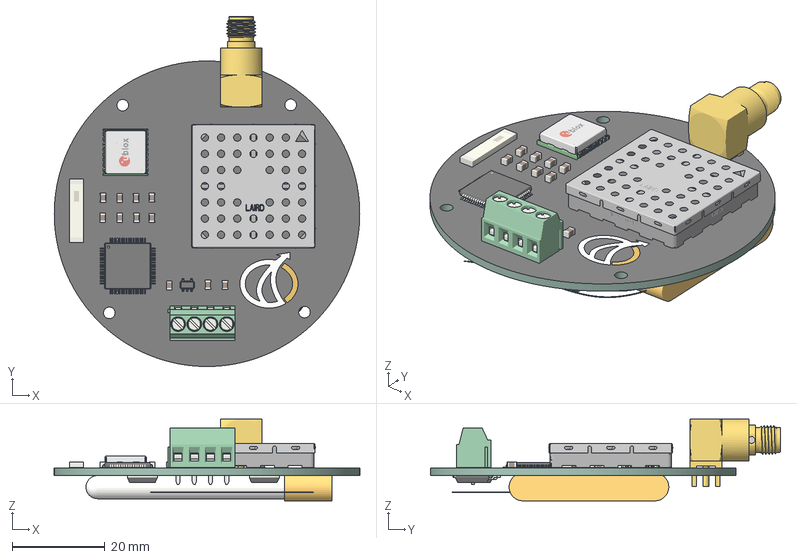
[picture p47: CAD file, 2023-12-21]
Presentation/WES0012-02_ASCII v7.3mf
66.0 x 75.6 x 17.7 mm

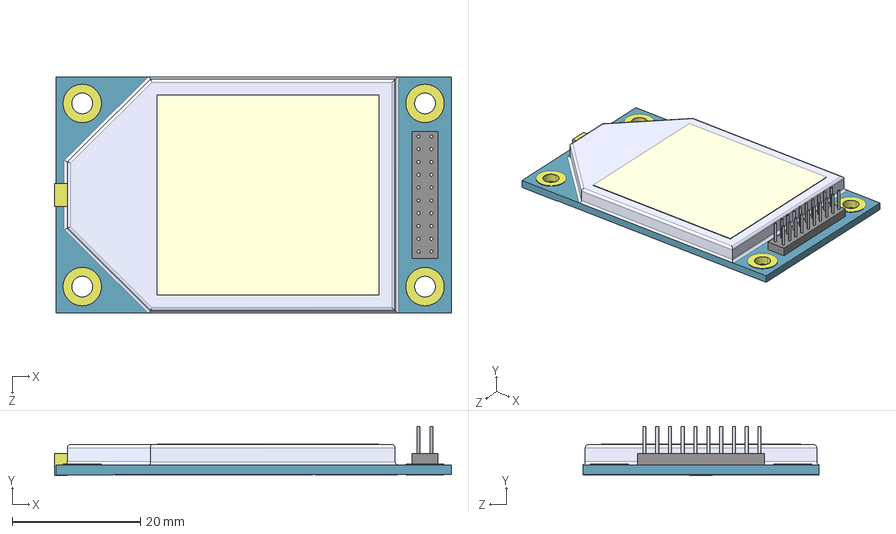
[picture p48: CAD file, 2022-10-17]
HW-Kicad/mainboard1/Components/9xtend/User Library-radio-1.STEP
62.0 x 7.67 x 36.9 mm

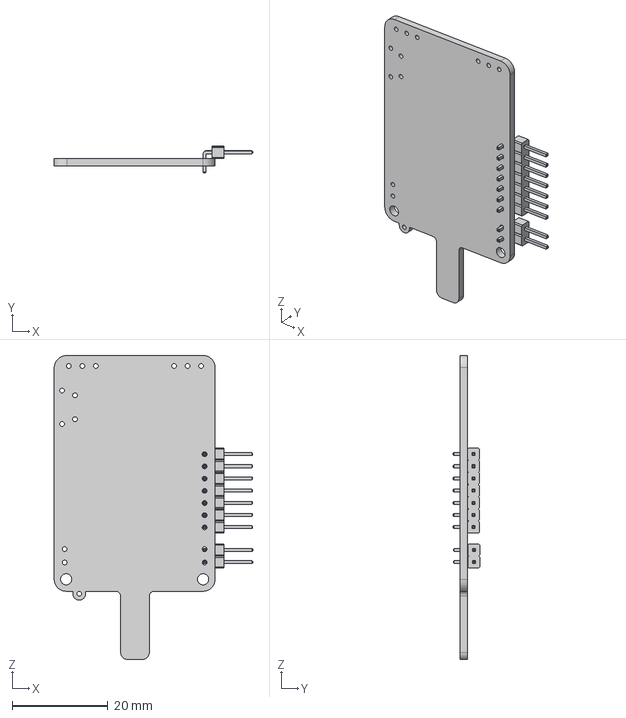
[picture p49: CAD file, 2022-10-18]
HW-Kicad/mainboard1/Components/LightAPRS/Component3.step
41.4 x 5.62 x 63.4 mm

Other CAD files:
HW-Kicad/batteryboard/Components/soportebaterias3d.stl

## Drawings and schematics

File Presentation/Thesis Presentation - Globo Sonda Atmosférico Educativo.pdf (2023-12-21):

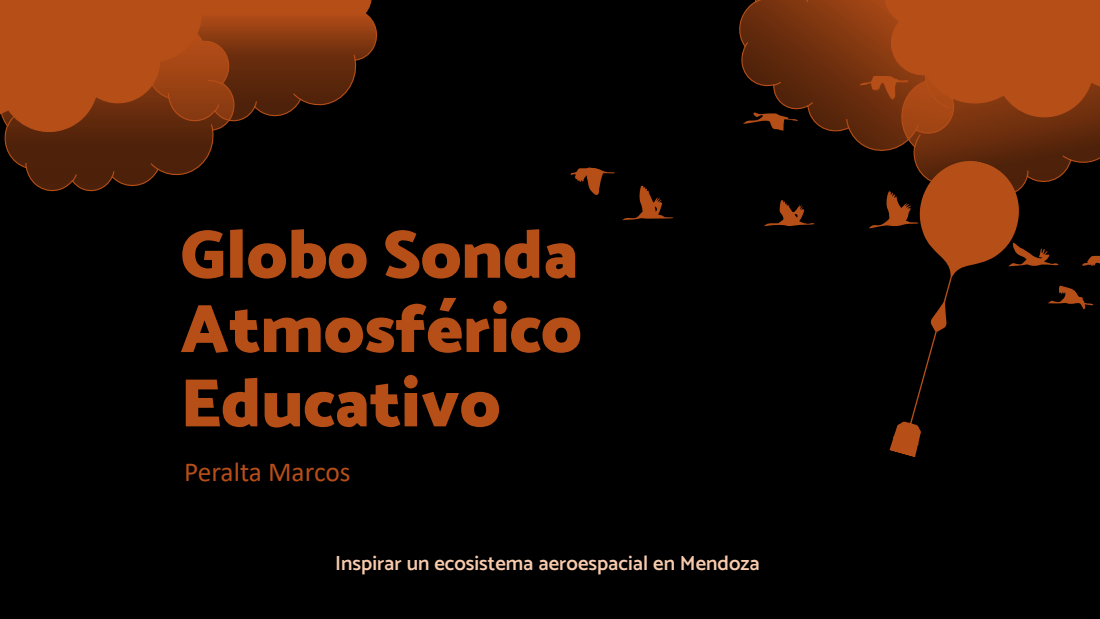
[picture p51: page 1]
Peralta Marcos; Globo Sonda Atmosférico Educativo

Inspirar un ecosistema aeroespacial en Mendoza

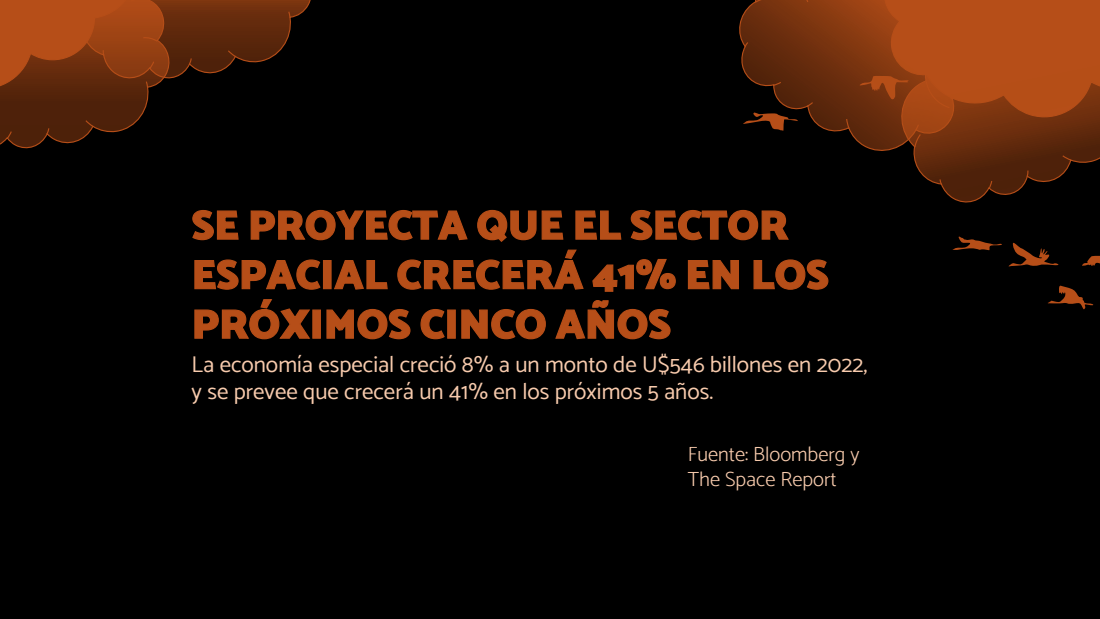
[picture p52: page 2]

SE PROYECTA QUE EL SECTOR
ESPACIAL CRECERÁ 41% EN LOS
PRÓXIMOS CINCO AÑOS
La economía especial creció 8% a un monto de U$546 billones en 2022,
y se prevee que crecerá un 41% en los próximos 5 años.

Fuente: Bloomberg y
The Space Report

# Globo Sonda

# Estado Actual

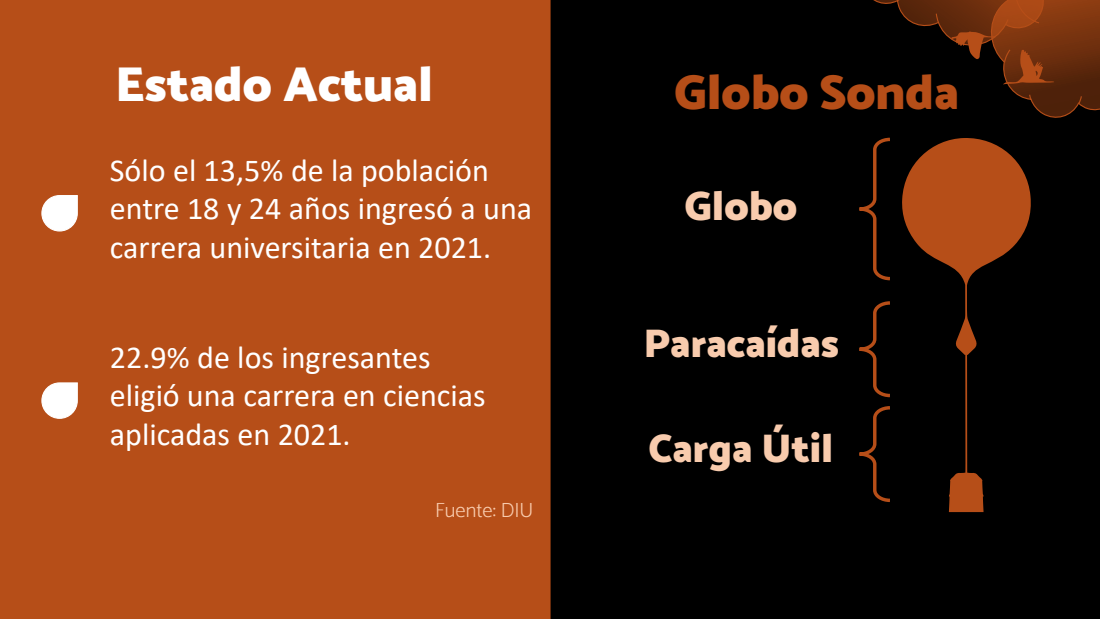
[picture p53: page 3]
Globo; Paracaídas; Carga Útil; Fuente: DIU

Sólo el 13,5% de la población
entre 18 y 24 años ingresó a una
carrera universitaria en 2021.

22.9% de los ingresantes
eligió una carrera en ciencias
aplicadas en 2021.

# Carga Útil

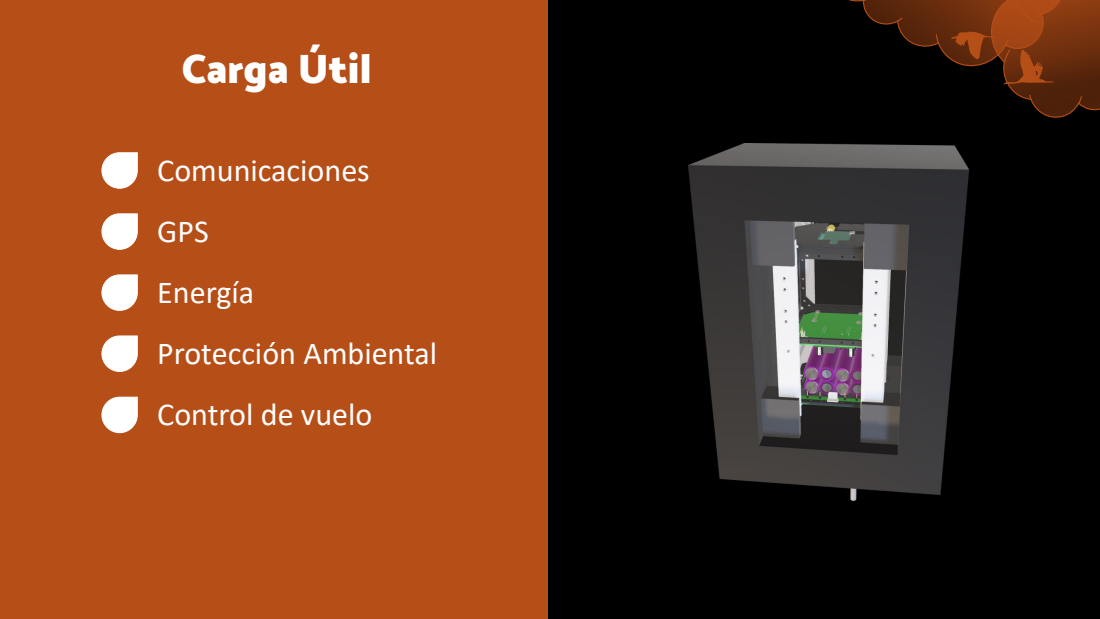
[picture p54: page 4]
Comunicaciones; GPS; Energía; Protección Ambiental

Control de vuelo

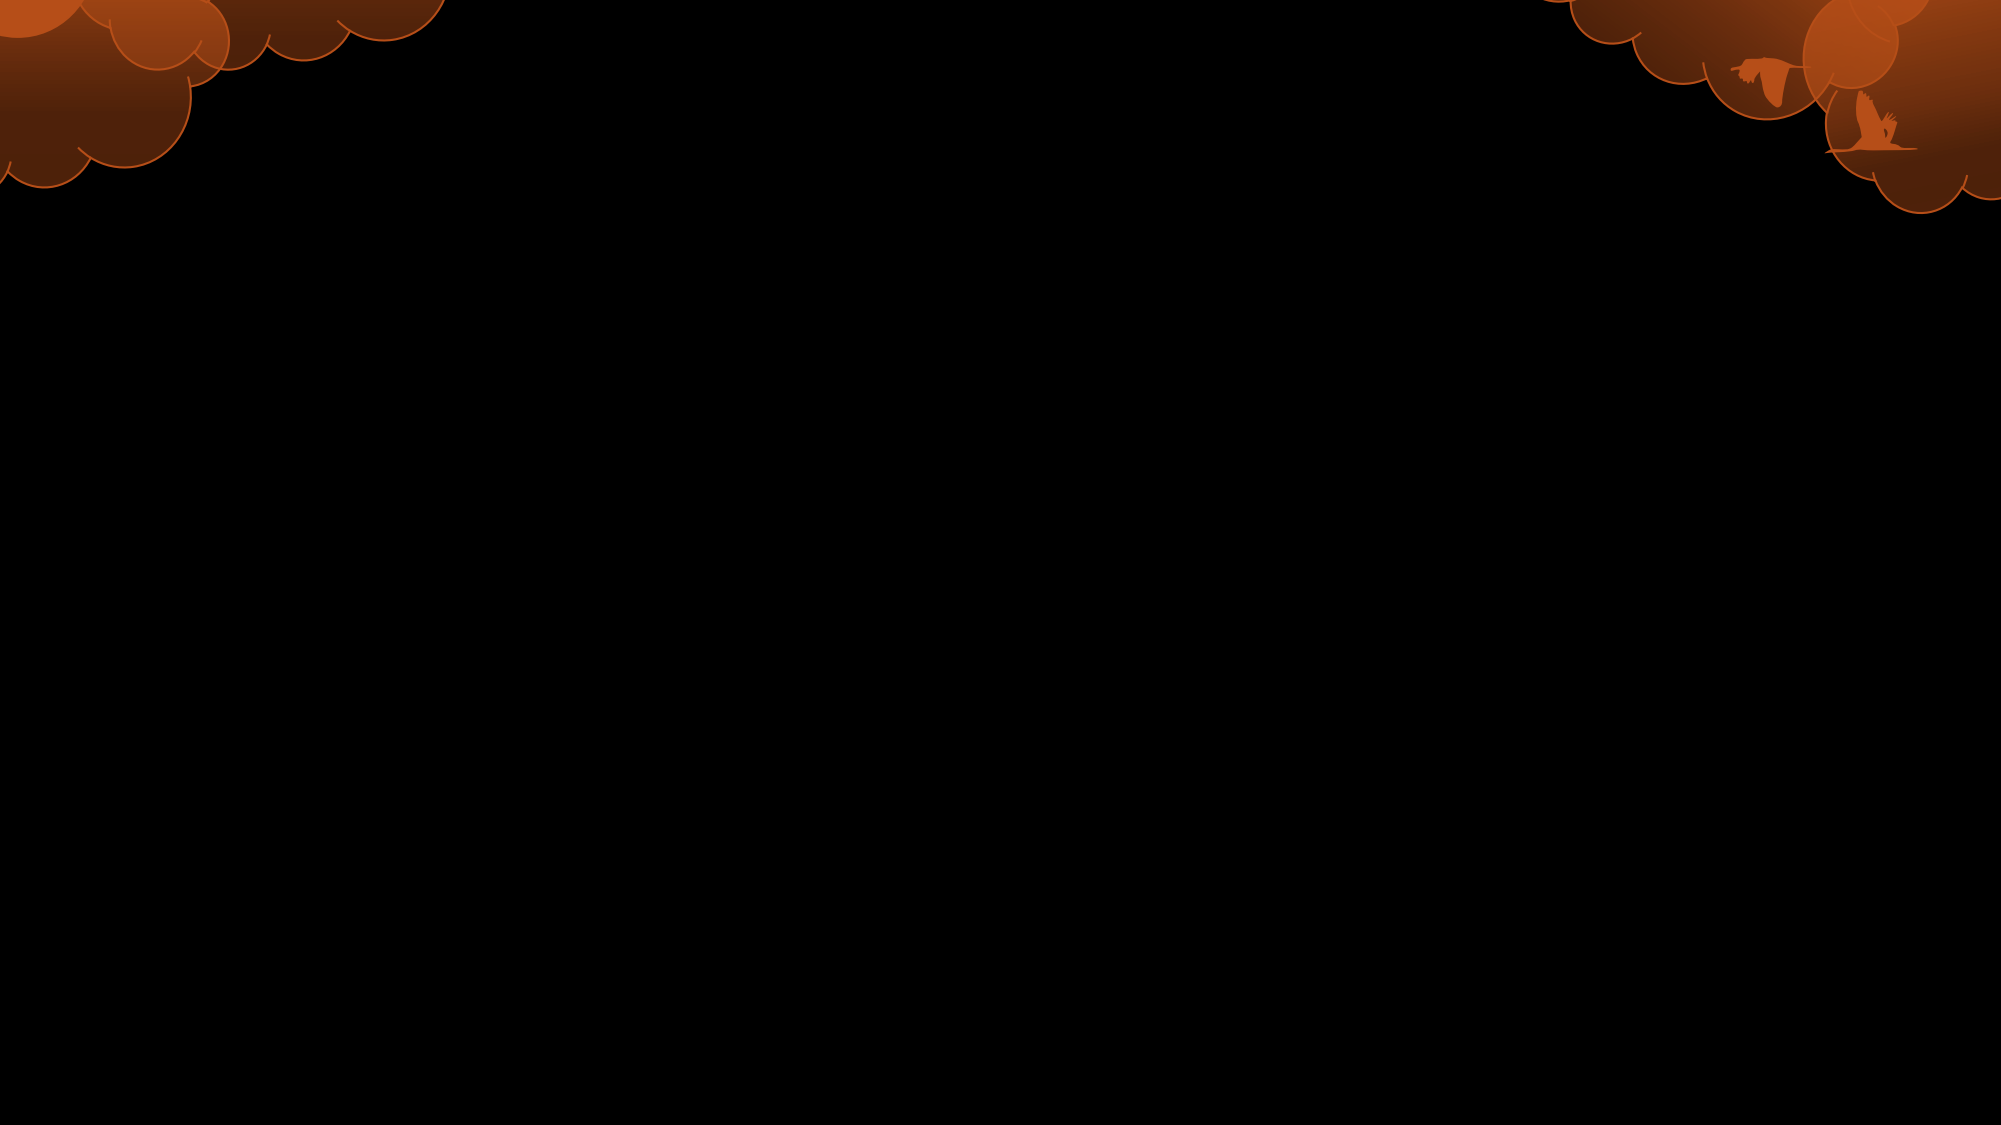
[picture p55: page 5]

# Resultados

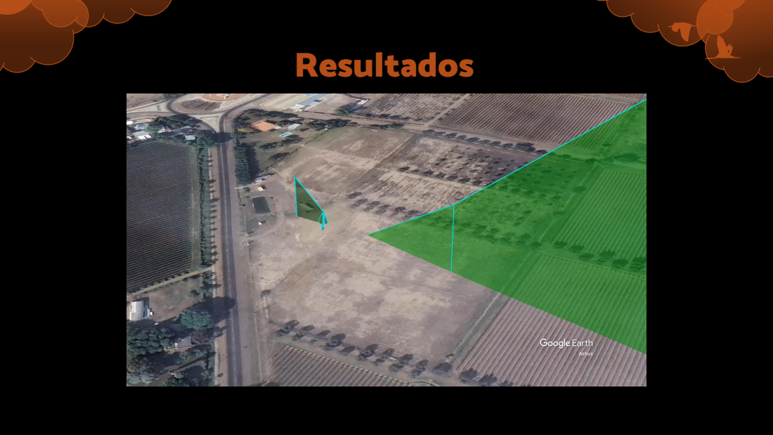
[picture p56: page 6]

# Resultados

# Temperaturas

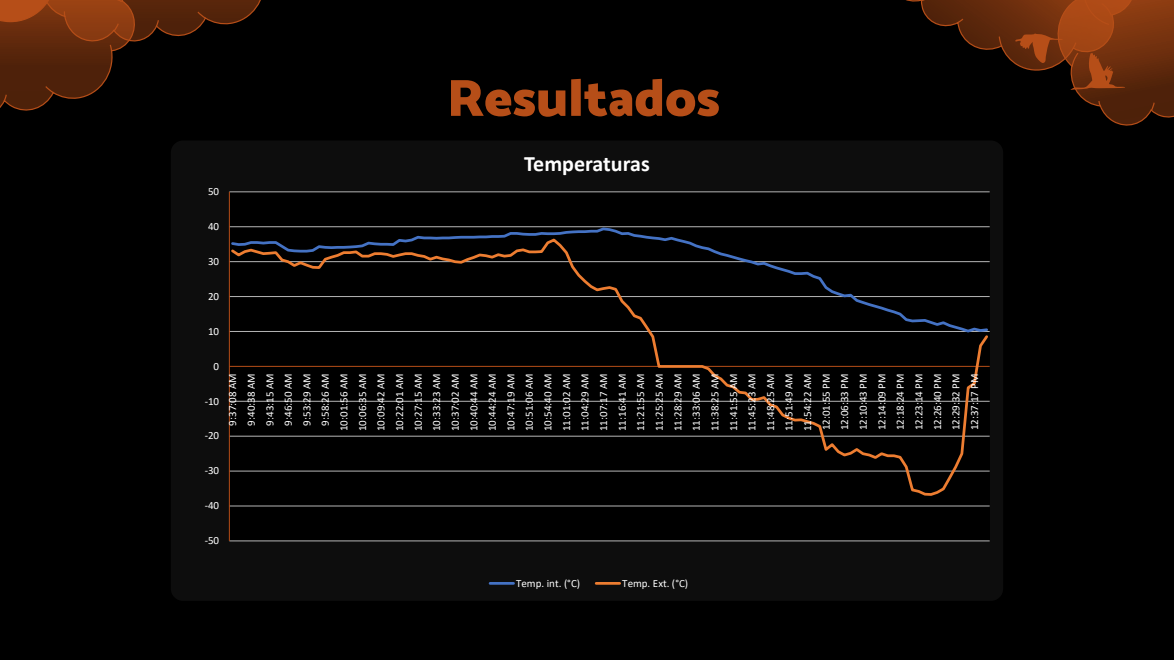
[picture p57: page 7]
Temp. int. (°C); Temp. Ext. (°C)

# Resultados

# Altura (m)

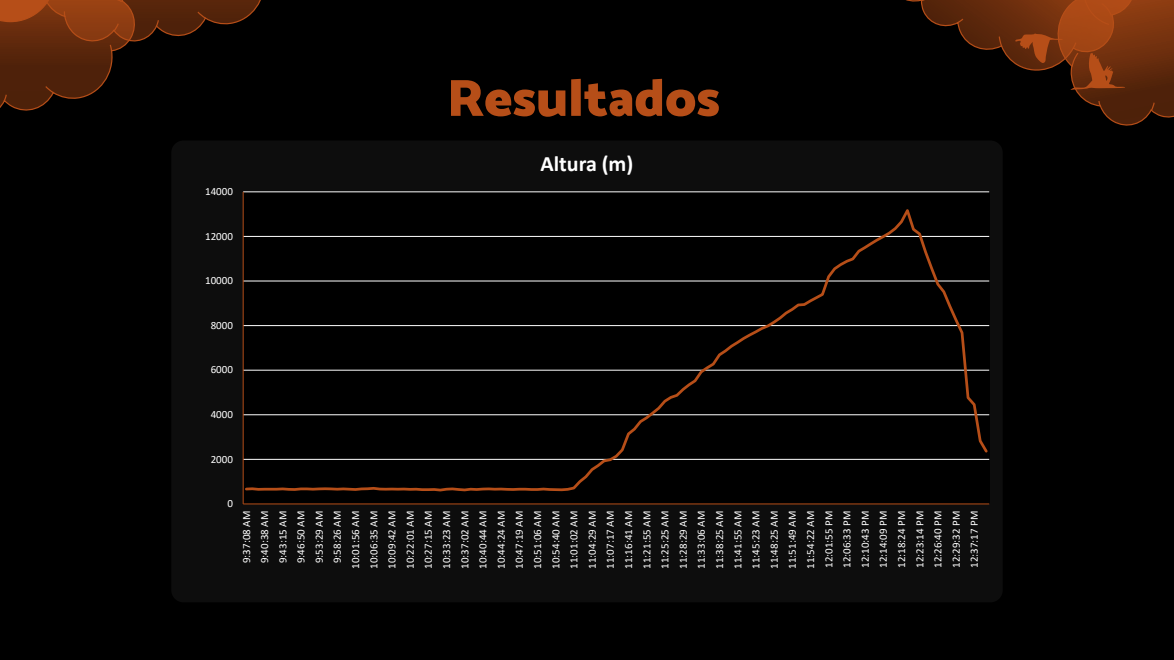
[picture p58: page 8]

# Resultados

# Velocidad vertical (m/s)

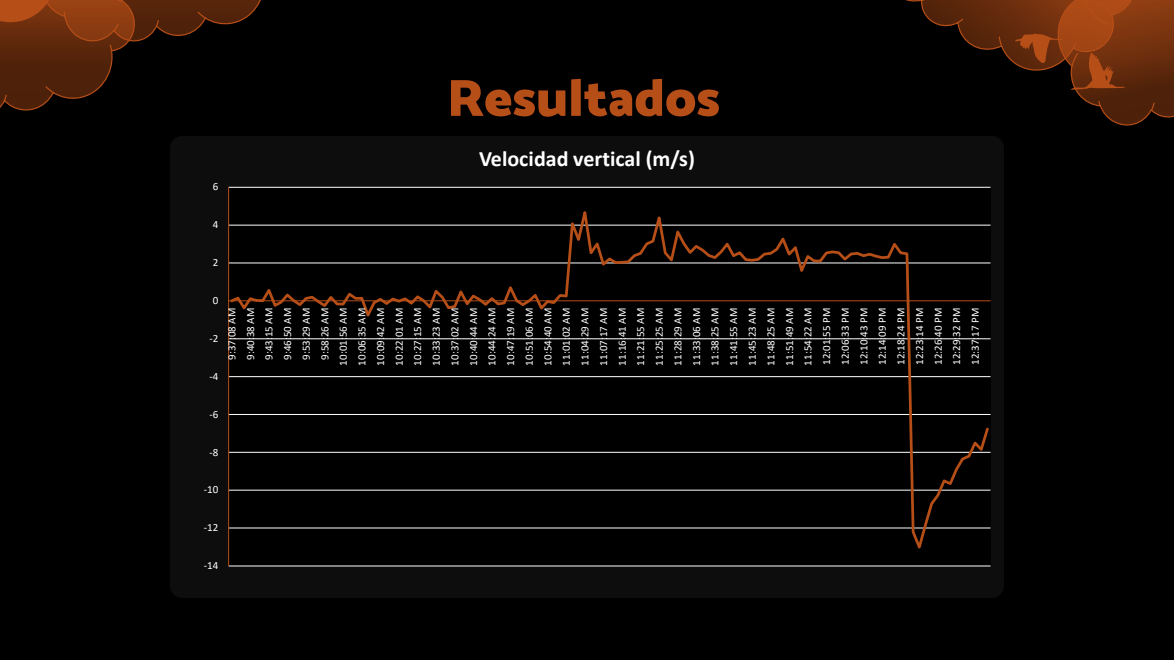
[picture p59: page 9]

# Productos Similares

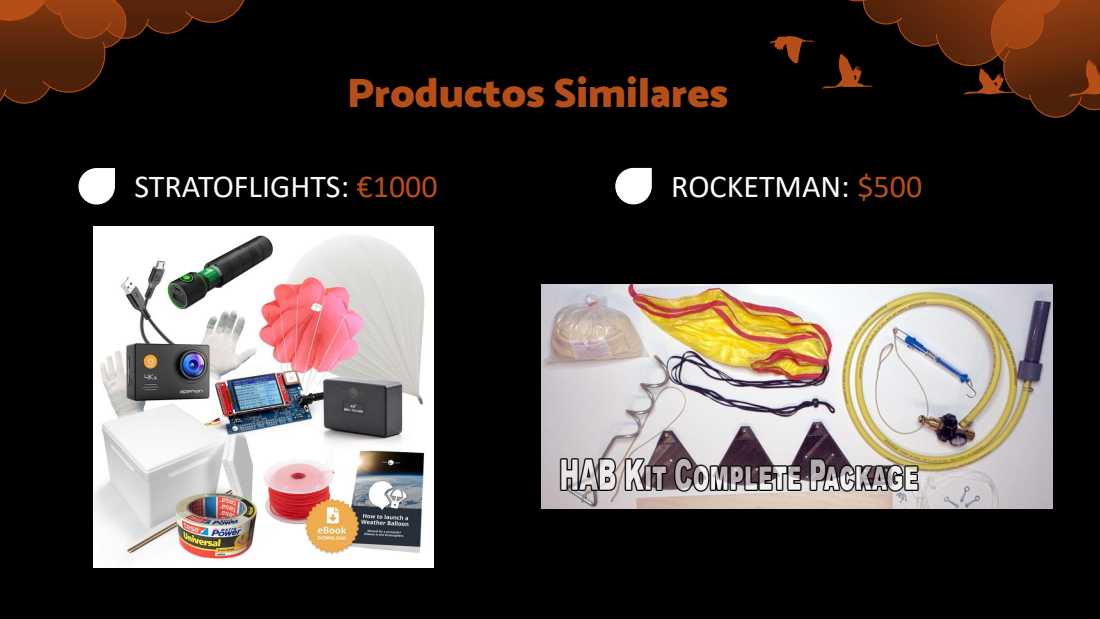
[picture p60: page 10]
STRATOFLIGHTS: €1000; ROCKETMAN: $500

# Modelo Económico

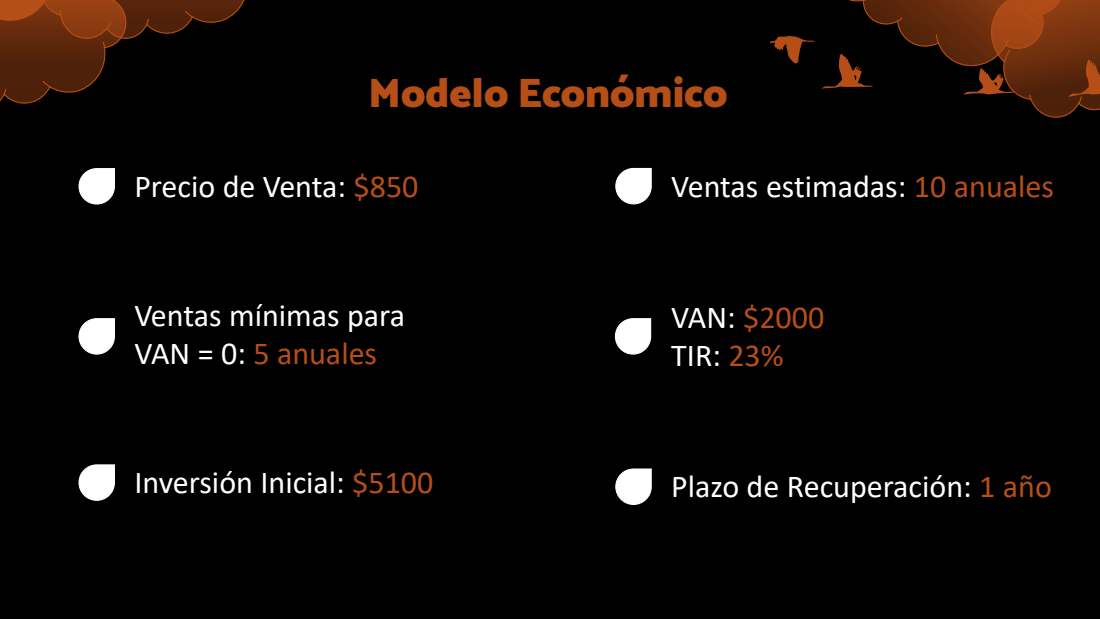
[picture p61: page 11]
VAN: $2000 TIR: 23%; Inversión Inicial: $5100; Plazo de Recuperación: 1 año

Precio de Venta: $850

Ventas estimadas: 10 anuales

Ventas mínimas para
VAN = 0: 5 anuales

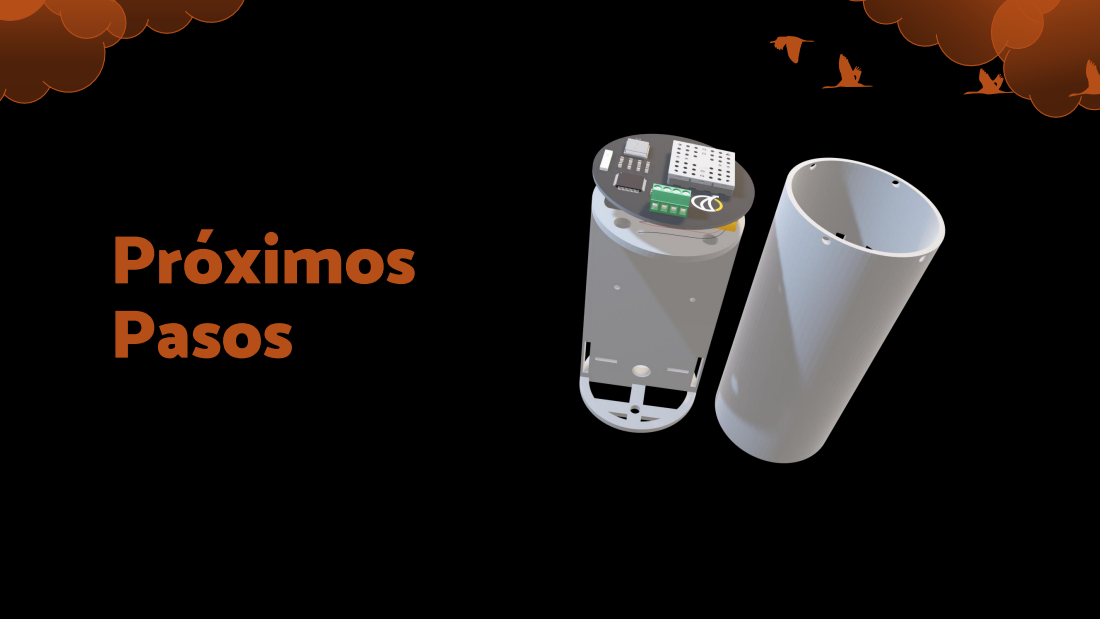
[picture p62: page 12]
Próximos Pasos

Próximos Pasos

Peralta Marcos; ¿Volamos?




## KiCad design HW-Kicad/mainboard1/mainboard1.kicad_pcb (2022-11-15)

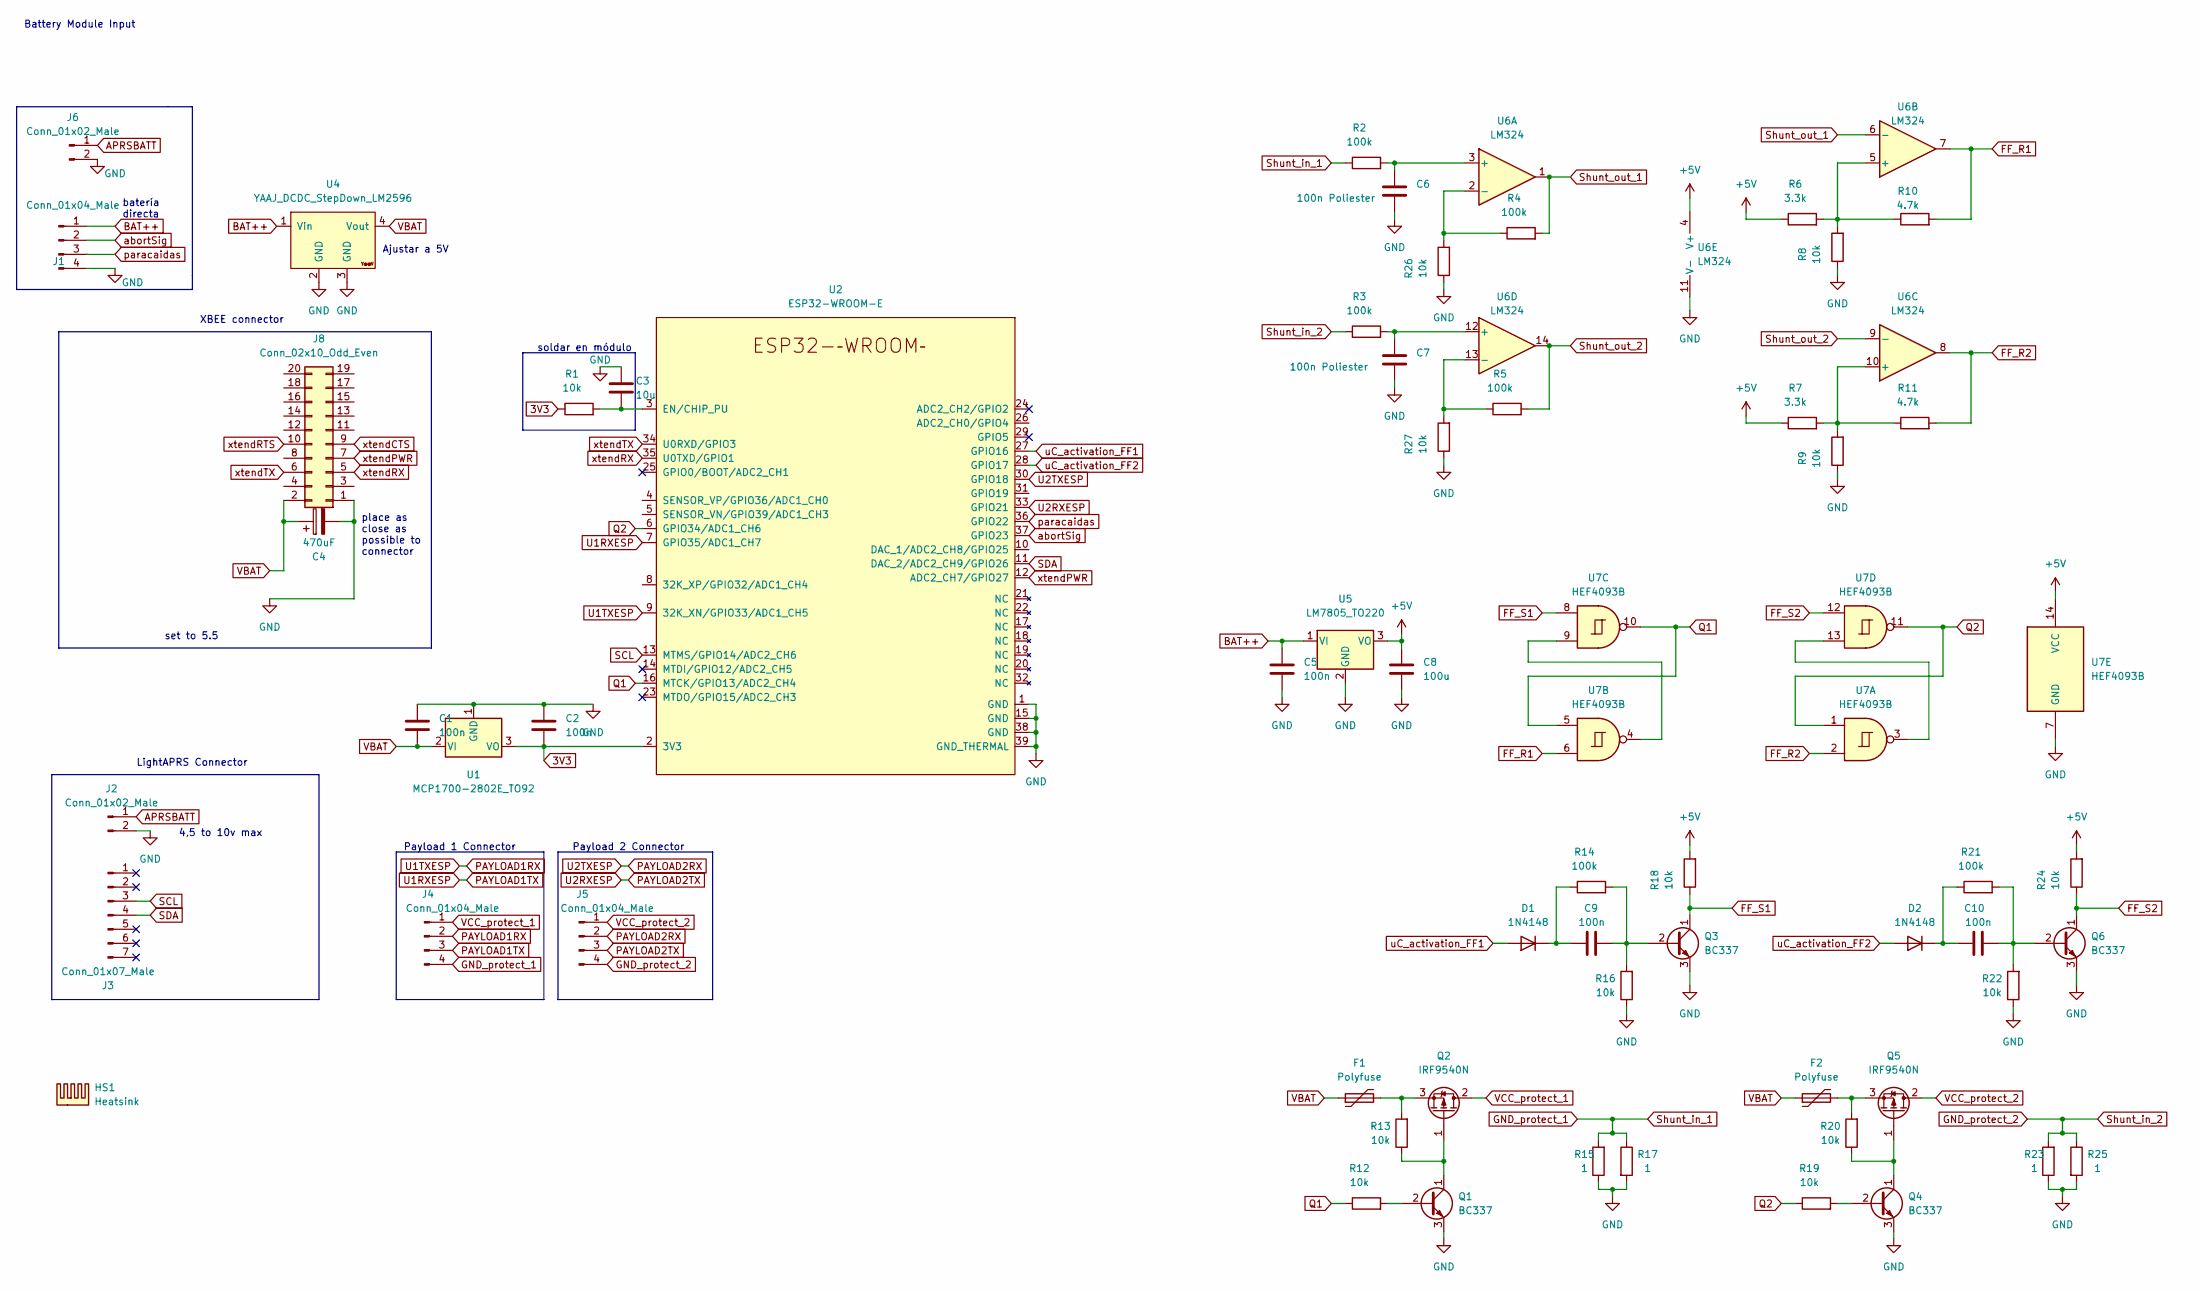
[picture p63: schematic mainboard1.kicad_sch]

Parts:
C1, C2, C5, C9, C10: 100n; C_Disc_D3.4mm_W2.1mm_P2.50mm
C3: 10u; CP_Radial_D4.0mm_P2.00mm
C4: 470uF; CP_Radial_D8.0mm_P3.80mm
C6, C7: 100n Poliester; C_Disc_D3.4mm_W2.1mm_P2.50mm
C8: 100u; CP_Radial_D6.3mm_P2.50mm
D1, D2: 1N4148; D_DO-35_SOD27_P7.62mm_Horizontal
F1, F2: Polyfuse; R_Axial_DIN0207_L6.3mm_D2.5mm_P5.08mm_Vertical
HS1: Heatsink; 9xtend
J1, J4, J5: Conn_01x04_Male; Molex_KK-254_AE-6410-04A_1x04_P2.54mm_Vertical
J2: Conn_01x02_Male; PinHeader_1x02_P2.54mm_Horizontal
J3: Conn_01x07_Male; PinHeader_1x07_P2.54mm_Horizontal
J6: Conn_01x02_Male; PinHeader_1x02_P2.54mm_Vertical
J8: Conn_02x10_Odd_Even; PinSocket_2x10_P2.00mm_Vertical
Q1, Q3, Q4, Q6: BC337; TO-92_Inline_Wide
Q2, Q5: IRF9540N; TO-220-3_Vertical
R1, R8, R9, R12, R13, R16, R18, R19, R20, R22, R24, R26, R27: 10k; R_Axial_DIN0207_L6.3mm_D2.5mm_P7.62mm_Horizontal
R2, R3, R4, R5, R14, R21: 100k; R_Axial_DIN0207_L6.3mm_D2.5mm_P7.62mm_Horizontal
R6, R7: 3.3k; R_Axial_DIN0207_L6.3mm_D2.5mm_P7.62mm_Horizontal
R10, R11: 4.7k; R_Axial_DIN0207_L6.3mm_D2.5mm_P7.62mm_Horizontal
R15, R17, R23, R25: 1; R_Axial_DIN0207_L6.3mm_D2.5mm_P7.62mm_Horizontal
U1: MCP1700-2802E_TO92; TO-92_Inline_Wide
U2: ESP32-WROOM-E; esp32_breakout
U4: YAAJ_DCDC_StepDown_LM2596; DC_DC_LM2596_small
U5: LM7805_TO220; TO-220-3_Vertical
U6: LM324; DIP-14_W7.62mm
U7: HEF4093B; DIP-14_W7.62mm

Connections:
3V3: C2.2, R1.1, U1.3 (VO), U2.2 (3V3)
+5V: C8.1, R6.1, R7.1, R18.2, R24.2, U5.3 (VO), U6.4 (V+), U7.14 (VCC)
APRSBATT: J2.1, J6.1
BAT++: C5.1, J1.1, U4.1 (Vin), U5.1 (VI)
FF_R1: R10.2, U6.7, U7.6
FF_R2: R11.2, U6.8, U7.2
FF_S1: Q3.1 (C), R18.1, U7.8
FF_S2: Q6.1 (C), R24.1, U7.12
GND: C1.1, C2.1, C3.1, C4.2, C5.2, C6.2, C7.2, C8.2, J1.4, J2.2, J6.2, J8.1, Q1.3 (E), Q3.3 (E), Q4.3 (E), Q6.3 (E), R8.1, R9.1, R15.1, R16.1, R17.2, R22.1, R23.1, R25.2, R26.1, R27.1, U1.1 (GND), U2.1 (GND), U2.15 (GND), U2.38 (GND), U2.39 (GND_THERMAL), U4.2 (GND), U4.3 (GND), U5.2 (GND), U6.11 (V-), U7.7 (GND)
GND_protect_1: J4.4, R2.1, R15.2, R17.1
GND_protect_2: J5.4, R3.1, R23.2, R25.1
unnamed: C3.2, R1.2, U2.3 (EN/CHIP_PU)
unnamed: C6.1, R2.2, U6.3 (+)
unnamed: C7.1, R3.2, U6.12 (+)
unnamed: C9.1, D1.1 (K), R14.1
unnamed: C9.2, Q3.2 (B), R14.2, R16.2
unnamed: C10.1, D2.1 (K), R21.1
unnamed: C10.2, Q6.2 (B), R21.2, R22.2
unnamed: F1.2, Q2.3 (S), R13.2
unnamed: F2.2, Q5.3 (S), R20.2
unnamed: Q1.1 (C), Q2.1 (G), R13.1
unnamed: Q1.2 (B), R12.2
unnamed: Q4.1 (C), Q5.1 (G), R20.1
unnamed: Q4.2 (B), R19.2
unnamed: R4.1, R26.2, U6.2 (-)
unnamed: R5.1, R27.2, U6.13 (-)
unnamed: R6.2, R8.2, R10.1, U6.5 (+)
unnamed: R7.2, R9.2, R11.1, U6.10 (+)
unnamed: U7.4, U7.9
unnamed: U7.3, U7.13
PAYLOAD1RX: J4.2, U2.9 (32K_XN/GPIO33/ADC1_CH5)
PAYLOAD1TX: J4.3, U2.7 (GPIO35/ADC1_CH7)
PAYLOAD2RX: J5.2, U2.30 (GPIO18)
PAYLOAD2TX: J5.3, U2.33 (GPIO21)
Q1: R12.1, U2.16 (MTCK/GPIO13/ADC2_CH4), U7.5, U7.10
Q2: R19.1, U2.6 (GPIO34/ADC1_CH6), U7.1, U7.11
SCL: J3.3, U2.13 (MTMS/GPIO14/ADC2_CH6)
SDA: J3.4, U2.11 (DAC_2/ADC2_CH9/GPIO26)
Shunt_out_1: R4.2, U6.1, U6.6 (-)
Shunt_out_2: R5.2, U6.9 (-), U6.14
VBAT: C1.2, C4.1, F1.1, F2.1, J8.2, U1.2 (VI), U4.4 (Vout)
VCC_protect_1: J4.1, Q2.2 (D)
VCC_protect_2: J5.1, Q5.2 (D)
abortSig: J1.2, U2.37 (GPIO23)
paracaidas: J1.3, U2.36 (GPIO22)
uC_activation_FF1: D1.2 (A), U2.27 (GPIO16)
uC_activation_FF2: D2.2 (A), U2.28 (GPIO17)
xtendCTS: J8.9
xtendPWR: J8.7, U2.12 (ADC2_CH7/GPIO27)
xtendRTS: J8.10
xtendRX: J8.5, U2.35 (U0TXD/GPIO1)
xtendTX: J8.6, U2.34 (U0RXD/GPIO3)

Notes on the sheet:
Payload 1 Connector
Battery Module Input
Ajustar a 5V
set to 5.5
4,5 to 10v max
XBEE connector
place as close as possible to connector
batería directa
soldar en módulo
Payload 2 Connector
LightAPRS Connector

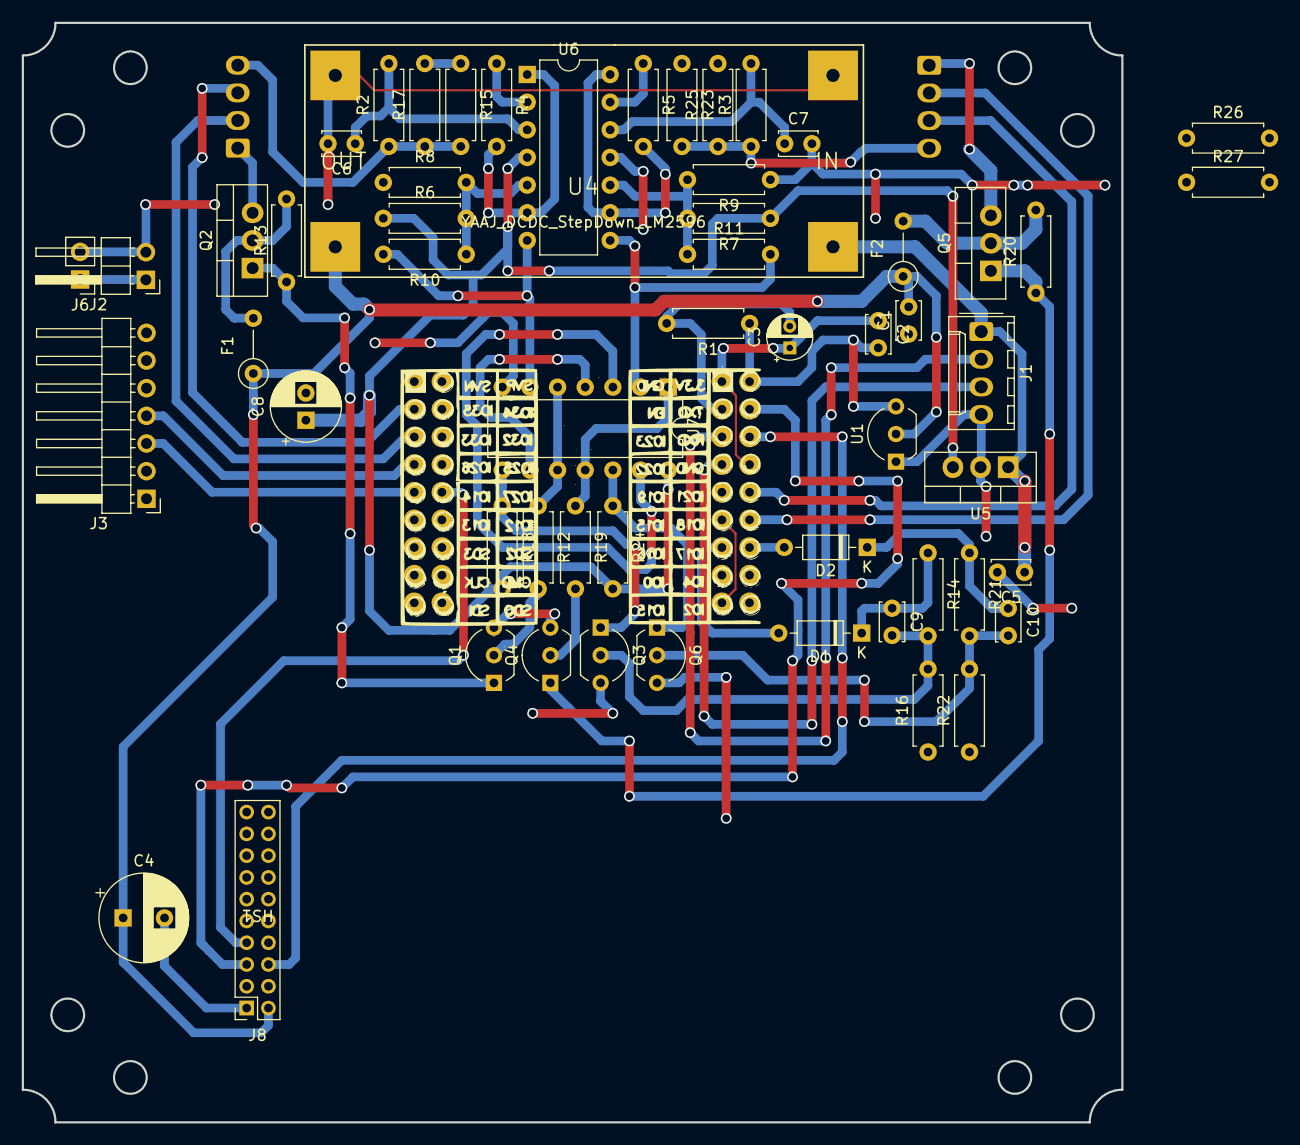
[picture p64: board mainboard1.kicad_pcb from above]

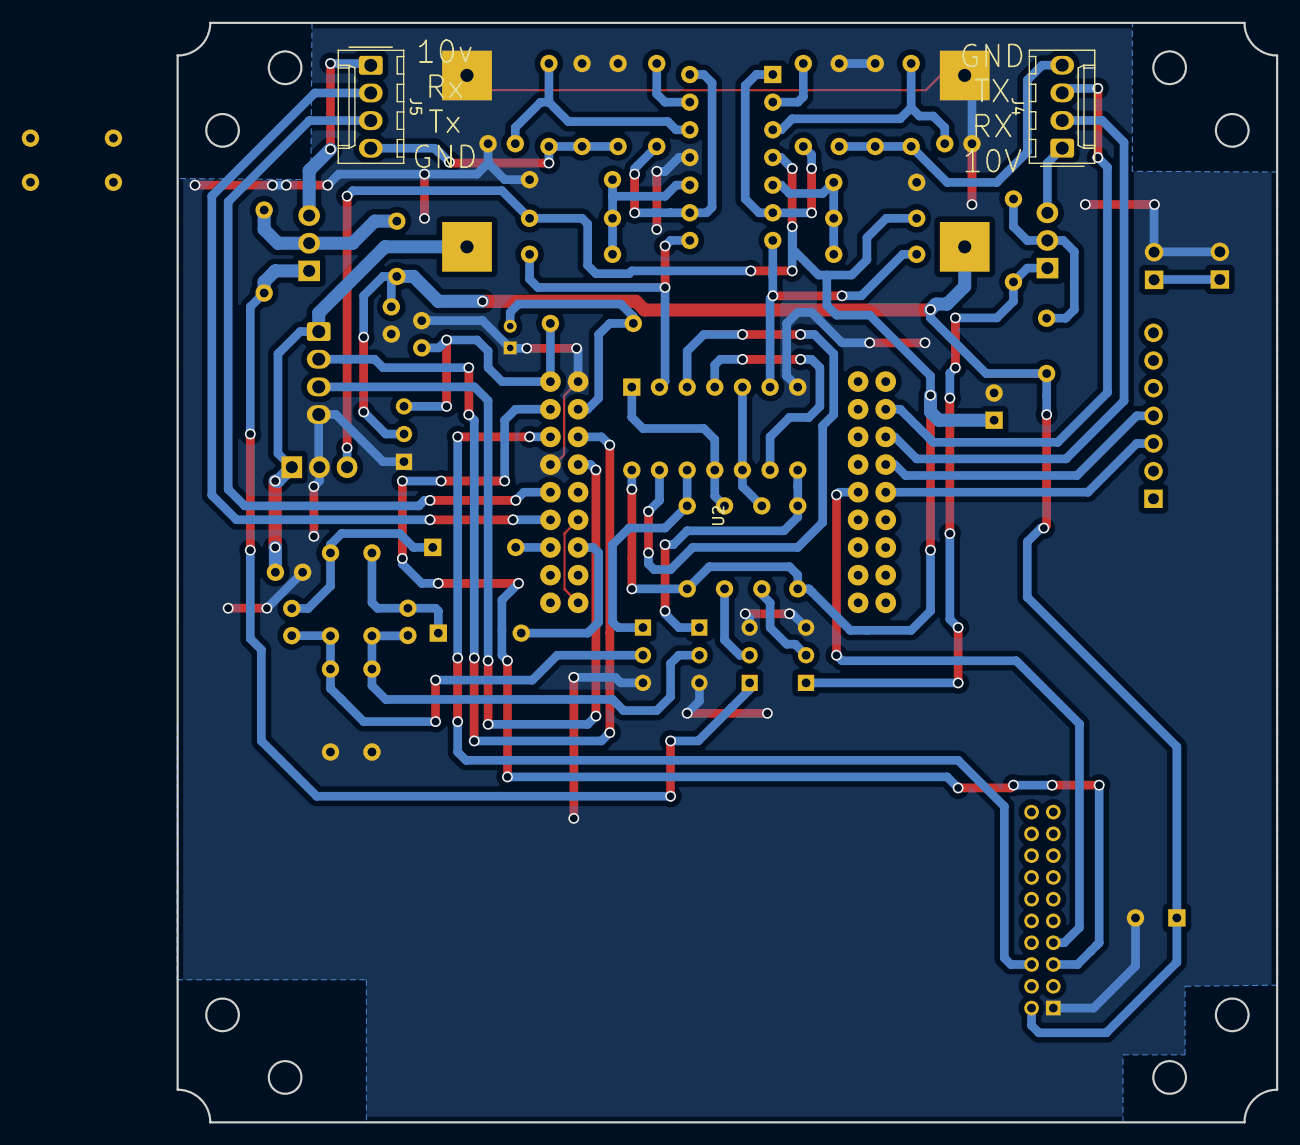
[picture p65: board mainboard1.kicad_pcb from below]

Board: 2 copper layers, 101.0 x 101.0 mm, 61 parts (2 on the bottom side), 50 nets.

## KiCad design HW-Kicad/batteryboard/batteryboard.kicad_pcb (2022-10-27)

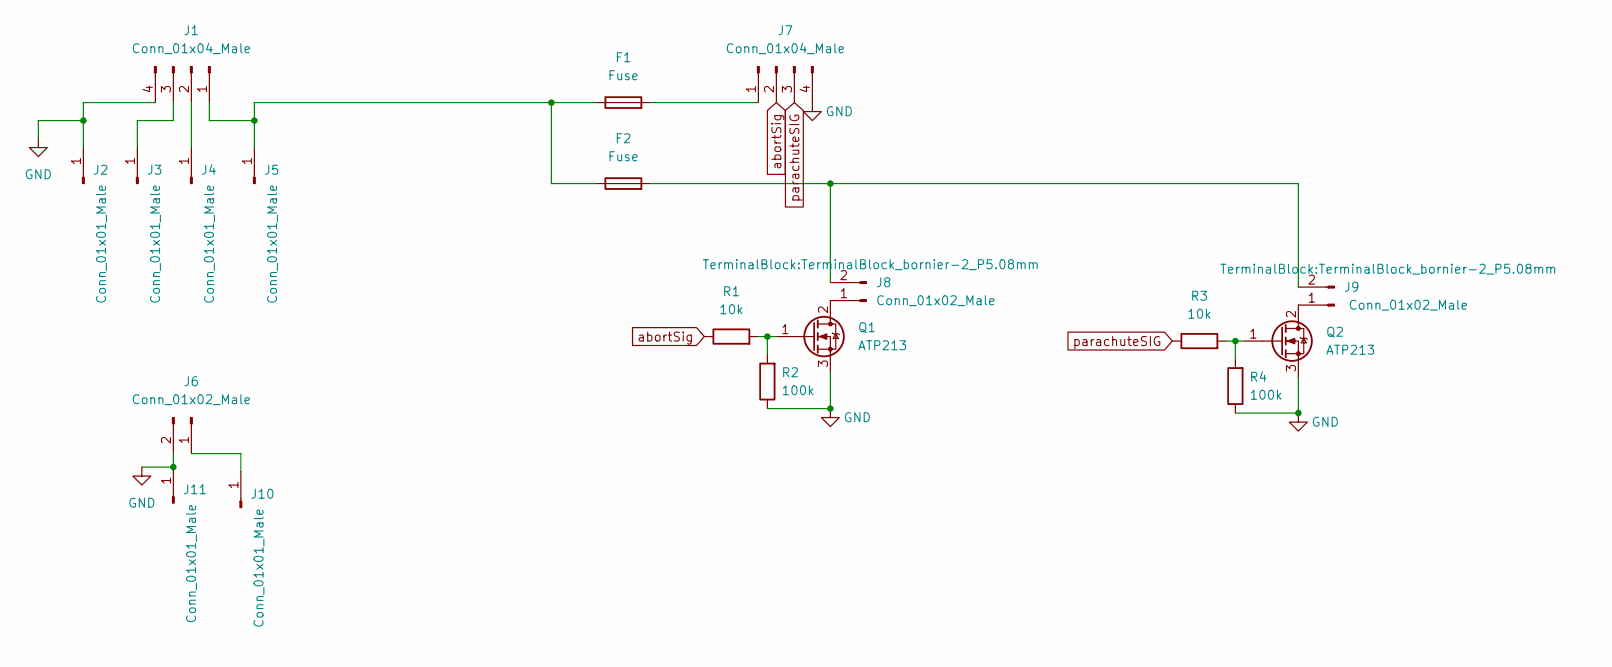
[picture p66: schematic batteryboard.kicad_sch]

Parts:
F1, F2: Fuse; Fuseholder_Blade_Mini_Keystone_3568
J1, J7: Conn_01x04_Male; Molex_KK-254_AE-6410-04A_1x04_P2.54mm_Vertical
J2, J3, J4, J5, J10, J11: Conn_01x01_Male; PinHeader_1x01_P2.54mm_Vertical
J6: Conn_01x02_Male; Molex_KK-254_AE-6410-02A_1x02_P2.54mm_Vertical
J8, J9: Conn_01x02_Male; TerminalBlock_bornier-2_P5.08mm
Q1, Q2: ATP213; TO-252-2
R1, R3: 10k; R_Axial_DIN0207_L6.3mm_D2.5mm_P10.16mm_Horizontal
R2, R4: 100k; R_Axial_DIN0207_L6.3mm_D2.5mm_P10.16mm_Horizontal

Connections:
GND: J1.4, J2.1, J6.2, J7.4, J11.1, Q1.3 (S), Q2.3 (S), R2.1, R4.1
unnamed: F1.1, F2.1, J1.1, J5.1
unnamed: F1.2, J7.1
unnamed: F2.2, J8.2, J9.2
unnamed: J1.2, J4.1
unnamed: J1.3, J3.1
unnamed: J8.1, Q1.2 (D)
unnamed: J9.1, Q2.2 (D)
unnamed: J6.1, J10.1
unnamed: Q1.1 (G), R1.2, R2.2
unnamed: Q2.1 (G), R3.2, R4.2
abortSig: J7.2, R1.1
parachuteSIG: J7.3, R3.1

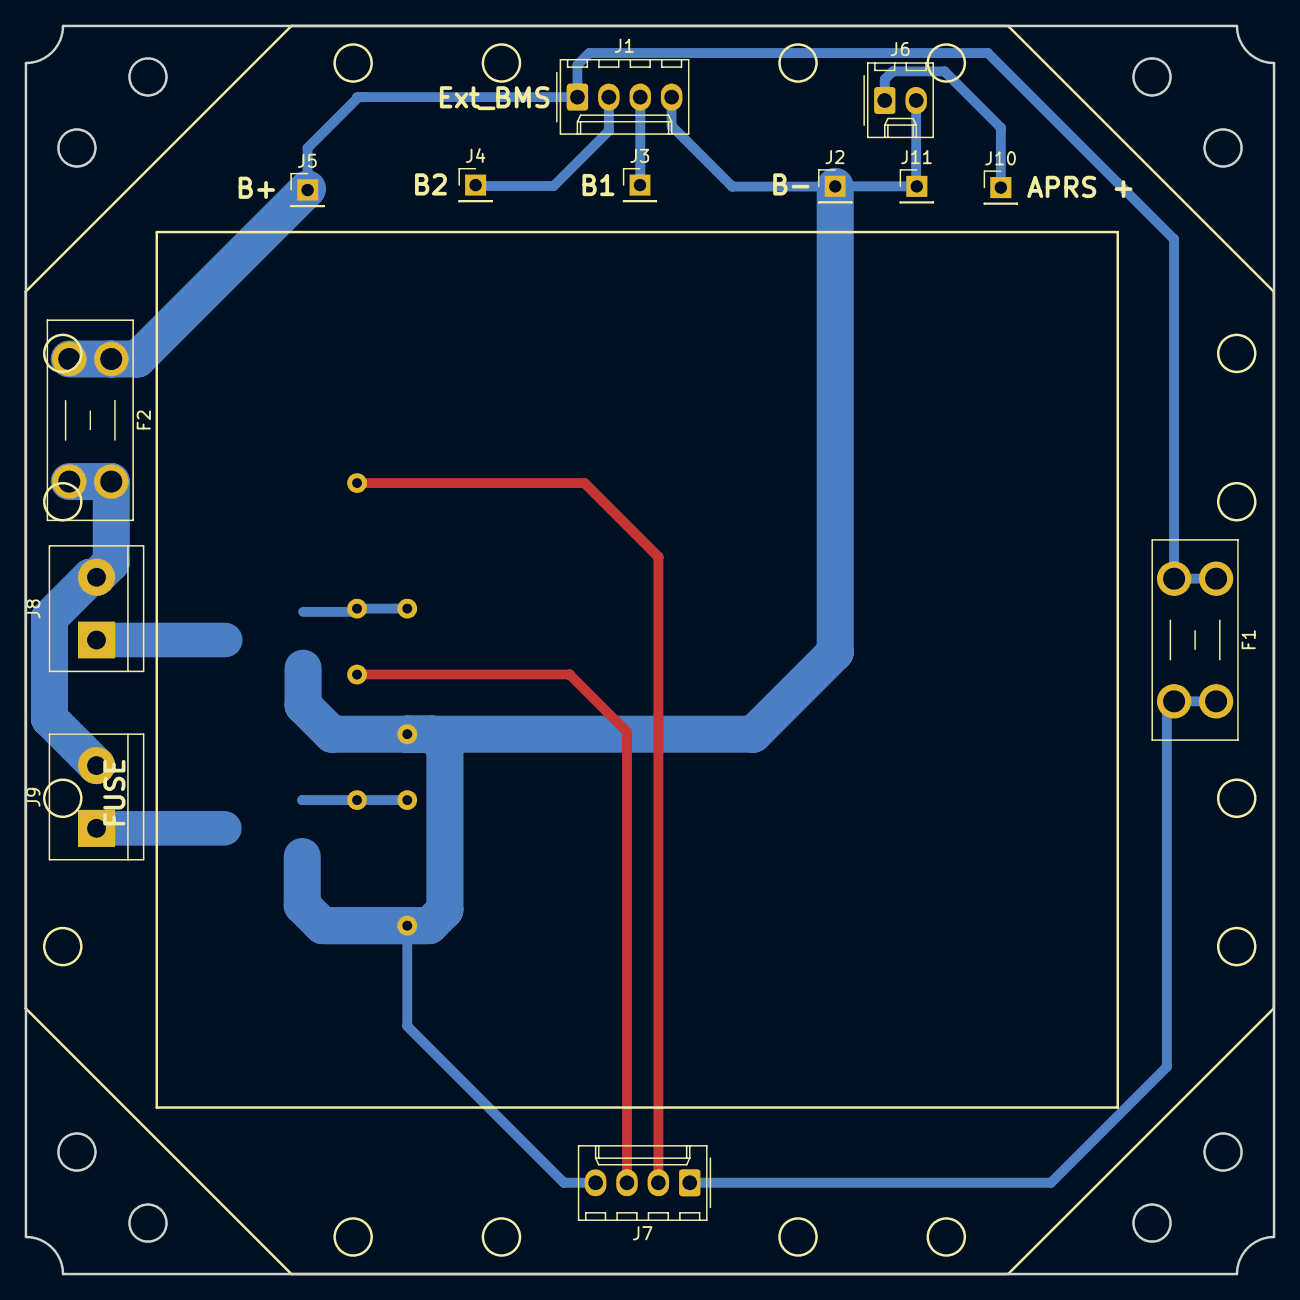
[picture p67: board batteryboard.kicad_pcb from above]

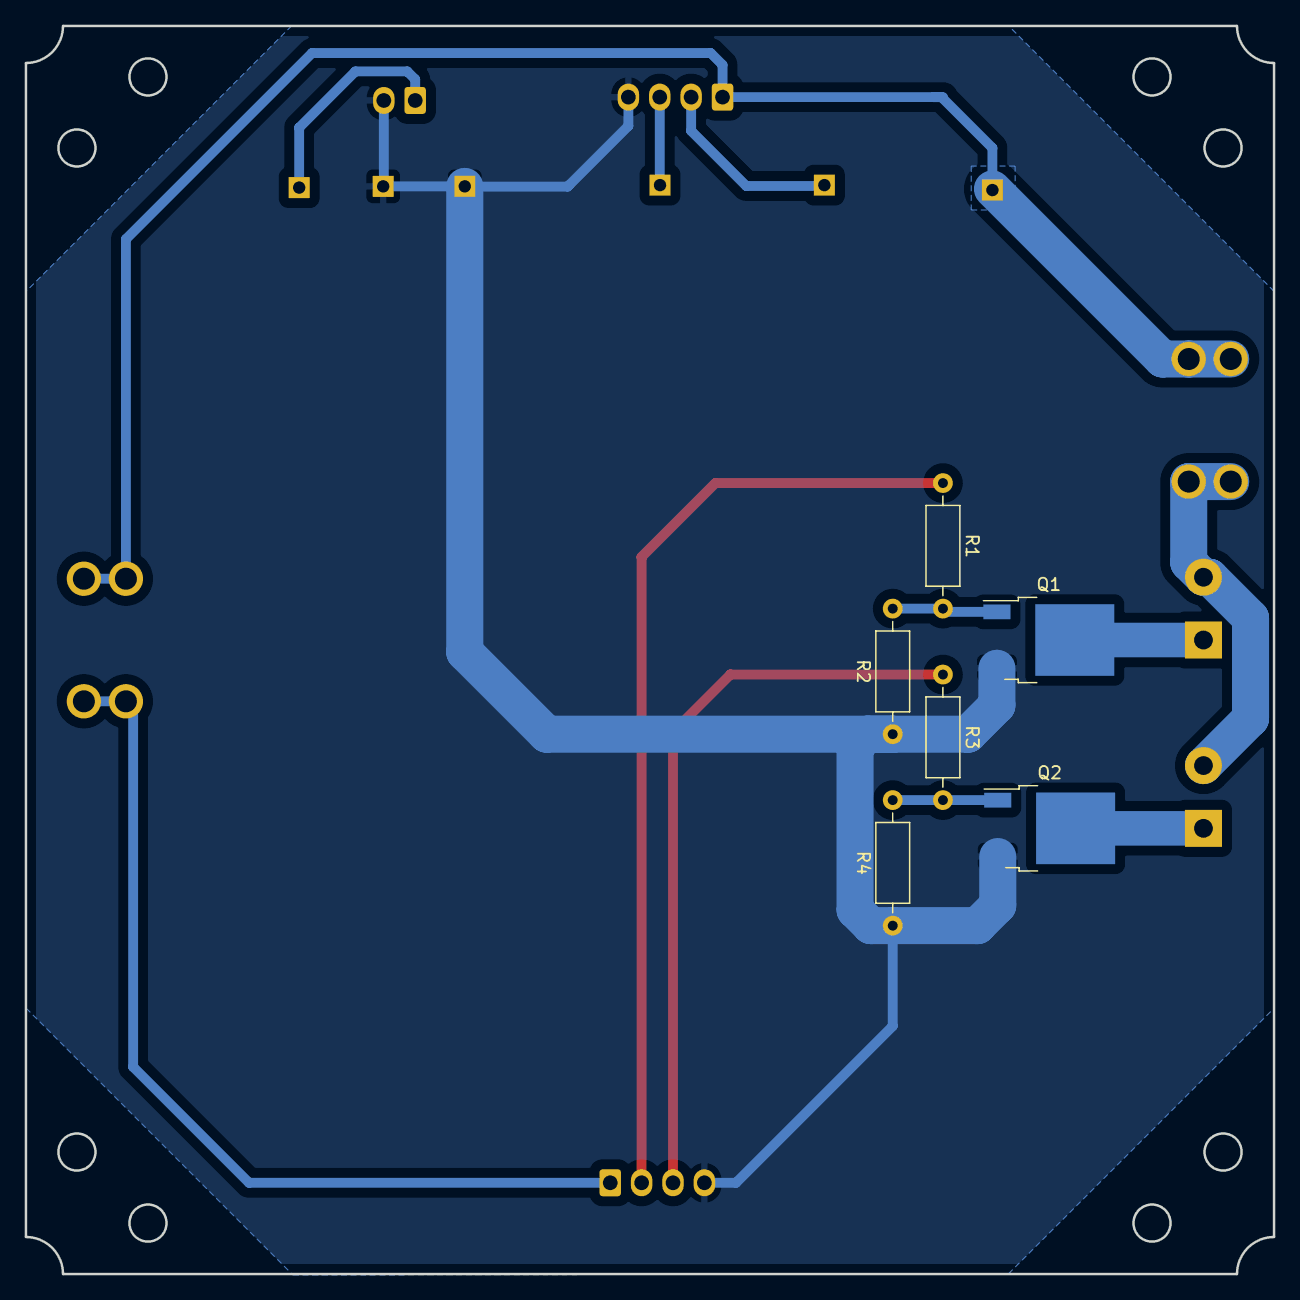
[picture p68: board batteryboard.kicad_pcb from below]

Board: 2 copper layers, 101.0 x 101.0 mm, 19 parts (6 on the bottom side), 13 nets.

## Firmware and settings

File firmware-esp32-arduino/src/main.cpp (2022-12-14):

/**
 * @file main.cpp
 * @author your name (you@domain.com)
 * @brief
 * @version 0.1
 * @date 2022-11-17
 *
 * @copyright Copyright (c) 2022
 *
 *
 */
// TODO: aumentar corriente en nicrom si no se detecta que el globo desciende.

#include <Arduino.h>
#include <Wire.h>
#include <Preferences.h>
#include "lightaprs.hpp"
#include <esp_task_wdt.h>

#define ESP32_ADDR 0x10

// 3 seconds WDT
#define WDT_TIMEOUT 10

#define PERIODO_TX_TMINUS 5000
#define PERIODO_TX_ASCENSO 5000
#define PERIODO_TX_DESCENSO 5000
#define PERIODO_TX_PARACAIDAS 5000
#define PERIODO_TX_RESCATE 5000

#define ALTURA_ASCENSO 2000
#define ALTURA_PARACAIDAS 10000

#define MAX_REINTENTOS_PAYLOADS 3

#define TIEMPO_MAX_SIN_KA 600000
#define ALTURA_MAX_VUELOS_COMERCIALES 12000

// 9xtend
#define XTEND_RX 1   // xtendRX
#define XTEND_TX 3   // xtendTX
#define XTEND_PWR 27 // xtendPWR

// payload1
#define PAYLOAD1_RX 35    // U1RXESP
#define PAYLOAD1_TX 33    // U1TXESP
#define PAYLOAD1_CHECK 13 // Q1
#define PAYLOAD1_ON 16    // uC_activation_FF1
#define PAYLOAD1_OFF 25

// payload2
#define PAYLOAD2_RX 21    // U2RXESP
#define PAYLOAD2_TX 18    // U2TXESP
#define PAYLOAD2_CHECK 34 // Q2
#define PAYLOAD2_ON 17    // uC_activation_FF2
#define PAYLOAD2_OFF 19

// lightaprs
#define LIGHTAPRS_SDA 14 // SDA
#define LIGHTAPRS_SCL 26 // SCL

// gpio
#define NICROM_PIN 23    // abortSig
#define PARACHUTE_PIN 22 // paracaidas

#define PIN_BATERIA 4

// Inicializaciones

Preferences memoria;

// variables globales

// int alturaParacaidas; //altura desde la cual desplegaremos el paracaídas en KM

uint8_t estadoVuelo = 0;

enum estadosVuelo
{
  t_minus,
  ascenso,
  descenso,
  paracaidas,
  rescate
};

String serial0data, serial1data, serial2data;

uint32_t distanciaMaxima;
float_t latitudInicial;
float_t longitudInicial;
float_t alturaAnterior;

lightaprs_t lightaprs;

uint8_t reintento_payload1, reintento_payload2;

bool once = true;

// temporizadores

uint32_t lastKAtime = 0;
uint32_t lastmillis = 0;
uint32_t lastmillis_nicrom = 0;

float vbat_esp, vbat_aprs;

// funciones propias
uint32_t getDistance(float flat1, float flon1, float flat2, float flon2); // calcula la distancia del gps respecto a las cooredenadas actuales
void checkUart(void);                                                     // reivsa los puertos uart
String getDB(void);                                                       // pregunta al módulo de comunicaciones los dbs de recepcción
void abortarVuelo(int pwm);
void apagar_nicrom(void);
bool estadoPayload1(void);
bool estadoPayload2(void);
void guardar_estadoVuelo(void);
void apagarPayloads(void);
void mantenerPayloadsON(void);
void encenderPayload1(void);
void encenderPayload2(void);
void apagarPayload1(void);
void apagarPayload2(void);
void desactivar_paracaidas(void);
void activar_paracaidas(void);
float tensionBateria(void);
void guardar_coord_iniciales(void);

void setup()
{
  // pines
  pinMode(XTEND_PWR, OUTPUT);
  digitalWrite(XTEND_PWR, HIGH);

  pinMode(PAYLOAD1_CHECK, INPUT);
  pinMode(PAYLOAD1_OFF, INPUT);
  pinMode(PAYLOAD1_ON, OUTPUT);
  digitalWrite(PAYLOAD1_ON, LOW);

  pinMode(PAYLOAD2_CHECK, INPUT);
  pinMode(PAYLOAD2_OFF, INPUT);
  pinMode(PAYLOAD2_ON, OUTPUT);
  digitalWrite(PAYLOAD2_ON, LOW);

  pinMode(NICROM_PIN, OUTPUT);
  digitalWrite(NICROM_PIN, LOW);
  pinMode(PARACHUTE_PIN, OUTPUT);
  digitalWrite(PARACHUTE_PIN, LOW);

  esp_task_wdt_init(WDT_TIMEOUT, true); // enable panic so ESP32 restarts
  esp_task_wdt_add(NULL);               // add current thread to WDT watch

  // comms
  Serial.begin(9600);
  Serial1.begin(9600, SERIAL_8N1, PAYLOAD1_RX, PAYLOAD1_TX);
  Serial2.begin(9600, SERIAL_8N1, LIGHTAPRS_SDA, LIGHTAPRS_SCL);
  // Wire.begin(ESP32_ADDR, LIGHTAPRS_SDA, LIGHTAPRS_SCL, 100000);

  Serial.println("Iniciando");

  // busco en memoria los datos relevantes al control del vuelo
  memoria.begin("vuelo", false);
  estadoVuelo = memoria.getUChar("estadoVuelo", 0);
  latitudInicial = memoria.getFloat("latitud", 0);
  longitudInicial = memoria.getFloat("longitud", 0);
  distanciaMaxima = memoria.getUInt("maxdist", 75000);
  memoria.end();
}

void loop()
{
  static int pwm = 30;
  switch (estadoVuelo)
  {
  case t_minus:
  {
    mantenerPayloadsON();
    checkUart();

    if (new_data_available())
    {
      read_last_received(&lightaprs);
      latitudInicial = lightaprs.latitud;
      longitudInicial = lightaprs.longitud;
      guardar_coord_iniciales();
    }

    if ((millis() - lastmillis) > PERIODO_TX_TMINUS)
    {
      lastmillis = millis();
      Serial.printf("[t-minus] Lat: %f, Lon: %f, Alt: %f, Temp_int: %.2f, Temp_ext: %.2f, Presion: %d, VBat_esp: %.2f, Vbat_aprs: %.2f\r\n", lightaprs.latitud, lightaprs.longitud, lightaprs.altura, lightaprs.temp_int, lightaprs.temp_ext, lightaprs.presion, vbat_esp, vbat_aprs);
    }

    if (lightaprs.altura > ALTURA_ASCENSO && lightaprs.altura > 0)
    {
      alturaAnterior = lightaprs.altura;
      estadoVuelo = ascenso;
      Serial.println("Estado de vuelo: ascenso");
      guardar_estadoVuelo();
    }

    break;
  }

  case ascenso:
  {
    mantenerPayloadsON();
    checkUart();

    if (new_data_available())
    {
      read_last_received(&lightaprs);
    }
    if ((millis() - lastmillis) > PERIODO_TX_ASCENSO)
    {
      lastmillis = millis();
      Serial.printf("[ascenso] Lat: %f, Lon: %f, Alt: %f, Temp_int: %.2f, Temp_ext: %.2f, Presion: %d, VBat_esp: %.2f, Vbat_aprs: %.2f\r\n", lightaprs.latitud, lightaprs.longitud, lightaprs.altura, lightaprs.temp_int, lightaprs.temp_ext, lightaprs.presion, vbat_esp, vbat_aprs);
    }
    if (lightaprs.latitud < 0 && lightaprs.longitud < 0)
    {
      if (getDistance(latitudInicial, longitudInicial, lightaprs.latitud, lightaprs.longitud) > distanciaMaxima)
      {
        if (once)
        {
          Serial.println("Limite superado - Vuelo abortado");
          once = false;
        }
        if ((millis() - lastmillis_nicrom) > 5000)
        {
          Serial.print("nicrom: ");
          Serial.println(pwm);
          abortarVuelo(pwm);
          pwm += 10;
          if (pwm > 255)
            pwm = 255;
          lastmillis_nicrom = millis();
        }
      }
    }

    // if (lightaprs.altura < ALTURA_MAX_VUELOS_COMERCIALES && (millis() - lastKAtime) > TIEMPO_MAX_SIN_KA)
    // {
    //   Serial.println("Comunicacion interrumpida - Vuelo abortado");
    //   abortarVuelo();
    // }

    if (lightaprs.altura <= (alturaAnterior - 500) && lightaprs.altura > 0)
    {
      alturaAnterior = lightaprs.altura;
      estadoVuelo = descenso;
      Serial.println("Estado de vuelo: descenso");
      guardar_estadoVuelo();
      once = true;
      pwm = 30;
    }
    else
    {
      alturaAnterior = lightaprs.altura;
    }

    break;
  }

  case descenso:
  {
    apagar_nicrom();
    mantenerPayloadsON();
    checkUart();

    if (new_data_available())
    {
      read_last_received(&lightaprs);
    }
    if ((millis() - lastmillis) > PERIODO_TX_DESCENSO)
    {
      lastmillis = millis();
      Serial.printf("[descenso] Lat: %f, Lon: %f, Alt: %f, Temp_int: %.2f, Temp_ext: %.2f, Presion: %d, VBat_esp: %.2f, Vbat_aprs: %.2f\r\n", lightaprs.latitud, lightaprs.longitud, lightaprs.altura, lightaprs.temp_int, lightaprs.temp_ext, lightaprs.presion, vbat_esp, vbat_aprs);
    }
    if (lightaprs.altura > (alturaAnterior + 500) && lightaprs.altura > 0)
    {
      alturaAnterior = lightaprs.altura;
      estadoVuelo = ascenso;
      Serial.println("Estado de vuelo: ascenso");
      guardar_estadoVuelo();
    }
    else if (lightaprs.altura < ALTURA_PARACAIDAS && lightaprs.altura > 0)
    {
      alturaAnterior = lightaprs.altura;
      estadoVuelo = paracaidas;
      Serial.println("Estado de vuelo: paracaidas");
      guardar_estadoVuelo();
    }
    else
    {
      alturaAnterior = lightaprs.altura;
    }

    break;
  }

  case paracaidas:
  {

    apagarPayloads();

    checkUart();

    if (new_data_available())
    {
      read_last_received(&lightaprs);
    }
    if ((millis() - lastmillis) > PERIODO_TX_PARACAIDAS)
    {
      lastmillis = millis();
      Serial.printf("[paracaidas] Lat: %f, Lon: %f, Alt: %f, Temp_int: %.2f, Temp_ext: %.2f, Presion: %d, VBat_esp: %.2f, Vbat_aprs: %.2f\r\n", lightaprs.latitud, lightaprs.longitud, lightaprs.altura, lightaprs.temp_int, lightaprs.temp_ext, lightaprs.presion, vbat_esp, vbat_aprs);
    }
    if (lightaprs.altura > (alturaAnterior + 500) && lightaprs.altura > 0)
    {
      alturaAnterior = lightaprs.altura;
      estadoVuelo = ascenso;
      Serial.println("Estado de vuelo: ascenso");
      guardar_estadoVuelo();
    }
    else if (lightaprs.altura <= ALTURA_ASCENSO && lightaprs.altura > 0)
    {
      estadoVuelo = rescate;
      Serial.println("Estado de vuelo: rescate");
      guardar_estadoVuelo();
    }
    else
    {
      alturaAnterior = lightaprs.altura;
    }
    break;
  }

  case rescate:
  {
    apagarPayloads();

    checkUart();

    if (new_data_available())
    {
      read_last_received(&lightaprs);
    }
    if ((millis() - lastmillis) > PERIODO_TX_RESCATE)
    {
      lastmillis = millis();
      Serial.printf("[rescate] Lat: %f, Lon: %f, Alt: %f, Temp_int: %.2f, Temp_ext: %.2f, Presion: %d, VBat_esp: %.2f, Vbat_aprs: %.2f\r\n", lightaprs.latitud, lightaprs.longitud, lightaprs.altura, lightaprs.temp_int, lightaprs.temp_ext, lightaprs.presion, vbat_esp, vbat_aprs);
    }
    break;
  }

  default:
    ESP.restart();
    break;
  }

  esp_task_wdt_reset();
}

float tensionBateria()
{
  float tension = analogRead(PIN_BATERIA) * 11.76 / 4095;
  return tension;
}

/**
 * @brief Función que verifica los puertos uart
 * Contesta el keep-alive de la estación terrena y también reenvia lo que tengan para reportar los payloads
 *
 */
void checkUart(void)
{
  vbat_esp = tensionBateria();
  int disponible = Serial2.available();
  if (disponible > 0)
  {
    receive_event(disponible, &vbat_aprs, vbat_esp);
  }

  String respuesta;
  if (Serial.available())
  {
    lastKAtime = millis();
    serial0data = Serial.readString();

    if (serial0data == "estado")
    {
      Serial.printf("[%d] dB: %s Lat: %f, Lon: %f, Alt: %f, Temp_int: %.2f, Temp_ext: %.2f, Presion: %d, VBat_esp: %.2f, Vbat_aprs: %.2f\r\n", estadoVuelo, getDB().c_str(), lightaprs.latitud, lightaprs.longitud, lightaprs.altura, lightaprs.temp_int, lightaprs.temp_ext, lightaprs.presion, vbat_esp, vbat_aprs);
      // Serial.printf("[%d] APRS: %d dB: %s Lat: %f, Lon: %f, Alt: %f, Temp_int: %f, Temp_ext: %f, Presion: %d\r\n", estadoVuelo, lightaprs_detected(), getDB().c_str(), lightaprs.latitud, lightaprs.longitud, lightaprs.altura, lightaprs.temp_int, lightaprs.temp_ext, lightaprs.presion);
    }
    else if (serial0data == "abort")
    {
      abortarVuelo(255);
      Serial.println("abortACK");
    }
    else if (serial0data.indexOf("nicromON: ") >= 0)
    {
      int pwm = serial0data.substring(10).toInt();
      if (pwm >= 0 && pwm < 256)
      {
        Serial.printf("PWM: %d\r\n", pwm);
        abortarVuelo(pwm);
      }
    }
    else if (serial0data == "abortOFF")
    {
      apagar_nicrom();
      Serial.println("abortOFFACK");
    }
    else if (serial0data == "paracaidasON")
    {
      activar_paracaidas();
      Serial.println("paracaidasONACK");
    }
    else if (serial0data == "paracaidasOFF")
    {
      desactivar_paracaidas();
      Serial.println("paracaidasOFFACK");
    }
    else if (serial0data == "payload1: ")
    {
      Serial1.print(serial0data.substring(10));
    }
    else if (serial0data == "payload2: ")
    {
      Serial2.print(serial0data.substring(10));
    }
    else if (serial0data == "payload1OFF")
    {
      apagarPayload1();
      Serial.println("payload1OFFACK");
    }
    else if (serial0data == "payload2OFF")
    {
      apagarPayload2();
      Serial.println("payload2OFFACK");
    }
    else if (serial0data == "payloadsOFF")
    {
      apagarPayloads();
      Serial.println("payloadsOFFACK");
    }
    else if (serial0data == "payload1ON")
    {
      encenderPayload1();
      Serial.println("payload1ONACK");
    }
    else if (serial0data == "payload2ON")
    {
      encenderPayload2();
      Serial.println("payload2ONACK");
    }
    else if (serial0data == "estadoPayloads")
    {
      Serial.printf("Payload1: %d, Payload2: %d\r\n", estadoPayload1(), estadoPayload2());
    }
    else if (serial0data.indexOf("distanciaMaxima: ") >= 0)
    {
      distanciaMaxima = serial0data.substring(17).toInt();
      Serial.printf("distanciaMaximaACK: %d\r\n", distanciaMaxima);
      memoria.putUInt("distanciaMaxima", distanciaMaxima);
    }
    else if (serial0data.indexOf("latitudInicial: ") >= 0)
    {
      latitudInicial = serial0data.substring(16).toFloat();
      Serial.printf("latitudInicialACK: %f\r\n", latitudInicial);
    }
    else if (serial0data.indexOf("longitudInicial: ") >= 0)
    {
      longitudInicial = serial0data.substring(17).toFloat();
      Serial.printf("longitudInicialACK: %f\r\n", longitudInicial);
    }
    else if (serial0data.indexOf("estadoVuelo: ") >= 0)
    {
      estadoVuelo = serial0data.substring(13).toInt();
      Serial.printf("estadoVueloACK: %d\r\n", estadoVuelo);
      guardar_estadoVuelo();
    }
    else if (serial0data == "restart")
    {
      Serial.println("RestartACK");
      ESP.restart();
    }
    else
    {
      Serial.println("Comando no reconocido");
    }
  }

  if (Serial1.available())
  {
    serial1data = Serial1.readString();
    Serial.printf("Payload1: %s", serial1data.c_str());
  }

  // if (Serial2.available())
  // {
  //   serial2data = Serial2.readString();
  //   Serial.printf("Payload2: %s", serial2data.c_str());
  // }
}

/**
 * @brief Función que le pide el módulo 9XTEND sus db's de recepción
 *
 * @return String la respuesta del módulo 9xtend en dbs
 */
String getDB(void)
{
  uint32_t lastmillis;

  String respuestaXtend;
  Serial.write("+++"); // entro en modo comandos

  lastmillis = millis();
  while (Serial.available() == 0 && (millis() - lastmillis) < 1000)
  { // espera que llegue la respuesta
  }
  Serial.readString();

  Serial.write("ATCF = 0\r"); // entro en modo comandos

  lastmillis = millis();
  while (Serial.available() == 0 && (millis() - lastmillis) < 1000)
  { // espera que llegue la respuesta
  }
  Serial.readString();

  Serial.write("ATPL:4\r"); // entro en modo comandos

  lastmillis = millis();
  while (Serial.available() == 0 && (millis() - lastmillis) < 1000)
  { // espera que llegue la respuesta
  }
  Serial.readString();

  Serial.write("ATDB\r"); // pregunto los db
  lastmillis = millis();
  while (Serial.available() == 0 && (millis() - lastmillis) < 1000)
  { // espera que llegue la respuesta
  }
  respuestaXtend = Serial.readString();

  // Serial.write("ATPL:4\r"); // configuro a 1W
  // lastmillis = millis();
  // while (Serial.available() == 0 && (millis() - lastmillis) < 1000)
  // { // espera que llegue la respuesta
  // }
  // check = Serial.readString();

  Serial.write("ATCN\r"); // salgo de modo comandos

  // delay(1000);

  // Serial.println(check);

  return respuestaXtend.substring(0, respuestaXtend.length() - 1); // devuelvo la respuesta de los db
}

/**
 * @brief Calcular la distancia entre dos puntos
 *
 * @param flat1 latitud
 * @param flon1 longitud
 * @param flat2 initiallatitud
 * @param flon2 initiallongitud
 * @return float Distancia en metros
 */
uint32_t getDistance(float flat1, float flon1, float flat2, float flon2)
{

  // Variables
  float dist_calc = 0;
  float dist_calc2 = 0;
  float diflat = 0;
  float diflon = 0;

  // Calculations
  diflat = radians(flat2 - flat1);
  flat1 = radians(flat1);
  flat2 = radians(flat2);
  diflon = radians((flon2) - (flon1));

  dist_calc = (sin(diflat / 2.0) * sin(diflat / 2.0));
  dist_calc2 = cos(flat1);
  dist_calc2 *= cos(flat2);
  dist_calc2 *= sin(diflon / 2.0);
  dist_calc2 *= sin(diflon / 2.0);
  dist_calc += dist_calc2;

  dist_calc = (2 * atan2(sqrt(dist_calc), sqrt(1.0 - dist_calc)));

  dist_calc *= 6371000; // Converting to meters

  return (uint32_t)dist_calc;
}

void abortarVuelo(int pwm)
{
  // digitalWrite(NICROM_PIN, HIGH);
  analogWrite(NICROM_PIN, pwm);
  analogWrite(PARACHUTE_PIN, pwm);
}

void apagar_nicrom(void)
{
  // digitalWrite(NICROM_PIN, LOW);
  analogWrite(NICROM_PIN, 0);
  analogWrite(PARACHUTE_PIN, 0);
}

void activar_paracaidas(void)
{
  digitalWrite(PARACHUTE_PIN, HIGH);
}

void desactivar_paracaidas(void)
{
  digitalWrite(PARACHUTE_PIN, LOW);
}

void encenderPayload1(void)
{
  if (!estadoPayload1())
  {
    digitalWrite(PAYLOAD1_ON, HIGH);
    delay(100);
    digitalWrite(PAYLOAD1_ON, LOW);
  }
}

void encenderPayload2(void)
{
  if (!estadoPayload2())
  {
    digitalWrite(PAYLOAD2_ON, HIGH);
    delay(100);
    digitalWrite(PAYLOAD2_ON, LOW);
  }
}

void mantenerPayloadsON(void)
{
  if (!estadoPayload1() && reintento_payload1 <= MAX_REINTENTOS_PAYLOADS)
  {
    digitalWrite(PAYLOAD1_ON, HIGH);
    delay(100);
    digitalWrite(PAYLOAD1_ON, LOW);
    reintento_payload1++;
  }
  if (!estadoPayload2() && reintento_payload2 <= MAX_REINTENTOS_PAYLOADS)
  {
    digitalWrite(PAYLOAD2_ON, HIGH);
    delay(100);
    digitalWrite(PAYLOAD2_ON, LOW);
    reintento_payload2++;
  }
}

void apagarPayload1(void) // descomentar cuando se corrija hardware
{
  if (estadoPayload1())
  {
    pinMode(PAYLOAD1_OFF, OUTPUT);
    digitalWrite(PAYLOAD1_OFF, LOW);
    delay(100);
    pinMode(PAYLOAD1_OFF, INPUT);
  }
}

void apagarPayload2(void) // descomentar cuando se corrija hardware
{
  if (estadoPayload2())
  {
    pinMode(PAYLOAD2_OFF, OUTPUT);
    digitalWrite(PAYLOAD2_OFF, LOW);
    delay(100);
    pinMode(PAYLOAD2_OFF, INPUT);
  }
}

void apagarPayloads(void)
{
  apagarPayload1();
  apagarPayload2();
}

bool estadoPayload1(void)
{
  return digitalRead(PAYLOAD1_CHECK);
}

bool estadoPayload2(void)
{
  return digitalRead(PAYLOAD2_CHECK);
}

void guardar_estadoVuelo(void)
{
  memoria.begin("vuelo", false);
  memoria.putUChar("estadoVuelo", estadoVuelo);
  memoria.end();
}

void guardar_coord_iniciales(void)
{
  memoria.begin("vuelo", false);
  memoria.putFloat("latitud", latitudInicial);
  memoria.putFloat("longitud", longitudInicial);
  memoria.end();
}

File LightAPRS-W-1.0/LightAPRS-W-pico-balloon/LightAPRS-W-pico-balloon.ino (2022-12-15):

#include <Arduino.h>
#include <Wire.h>
#include <SoftwareSerial.h>
#include <avr/wdt.h>
#include <GEOFENCE.h>          // Modified version of https://github.com/TomasTT7/TT7F-Float-Tracker/blob/master/Software/ARM_GEOFENCE.c
#include <LibAPRS.h>           //Modified version of https://github.com/markqvist/LibAPRS
#include <TinyGPS++.h>         //https://github.com/mikalhart/TinyGPSPlus
#include <LowPower.h>          //https://github.com/rocketscream/Low-Power
#include <Adafruit_BMP085.h>   //https://github.com/adafruit/Adafruit-BMP085-Library
#include <si5351.h>            //https://github.com/etherkit/Si5351Arduino
#include <JTEncode.h>          //https://github.com/etherkit/JTEncode (JT65/JT9/JT4/FT8/WSPR/FSQ Encoder Library)
#include <TimeLib.h>           //https://github.com/PaulStoffregen/Time
#include <TimerThree.h>        //https://github.com/PaulStoffregen/TimerThree/
#include <OneWire.h>           //https://github.com/PaulStoffregen/OneWire
#include <DallasTemperature.h> //https://github.com/milesburton/Arduino-Temperature-Control-Library
#include <SoftwareSerial.h>

#define DS18B20_PIN 7
#define ESP32_RX 6
#define ESP32_TX 5

typedef union
{
  int32_t entero;
  float flotante;
  uint8_t bytes[4];
} floatunion_t;

floatunion_t latt, lon, alt, temp_int, temp_ext, pres, vbat;

#define RfPDPin 19
#define GpsVccPin 18
#define RfPwrHLPin 21
#define RfPttPin 20
#define SiVccPin 0
#define BattPin A2
#define PIN_DRA_RX 22
#define PIN_DRA_TX 23

#define ADC_REFERENCE REF_3V3
#define OPEN_SQUELCH false

#define GpsON digitalWrite(GpsVccPin, LOW) // PNP
#define GpsOFF digitalWrite(GpsVccPin, HIGH)
#define RfON digitalWrite(RfPDPin, HIGH)
#define RfOFF digitalWrite(RfPDPin, LOW)
#define RfPwrHigh pinMode(RfPwrHLPin, INPUT)
#define RfPwrLow               \
  pinMode(RfPwrHLPin, OUTPUT); \
  digitalWrite(RfPwrHLPin, LOW)
#define RfPttON digitalWrite(RfPttPin, HIGH) // NPN
#define RfPttOFF digitalWrite(RfPttPin, LOW)
#define SiON digitalWrite(SiVccPin, HIGH) // NPN
#define SiOFF digitalWrite(SiVccPin, LOW)
#define AprsPinInput  \
  pinMode(12, INPUT); \
  pinMode(13, INPUT); \
  pinMode(14, INPUT); \
  pinMode(15, INPUT)
#define AprsPinOutput  \
  pinMode(12, OUTPUT); \
  pinMode(13, OUTPUT); \
  pinMode(14, OUTPUT); \
  pinMode(15, OUTPUT)

#define DEVMODE // Development mode. Uncomment to enable for debugging.
// #define WSPR // Uncomment to enable WSPR

//******************************  APRS CONFIG **********************************
char CallSign[7] = "LU1MUM";       // DO NOT FORGET TO CHANGE YOUR CALLSIGN
int8_t CallNumber = 11;            // SSID http://www.aprs.org/aprs11/SSIDs.txt
char Symbol = 'O';                 // '/O' for balloon, '/>' for car, for more info : http://www.aprs.org/symbols/symbols-new.txt
bool alternateSymbolTable = false; // false = '/' , true = '\'

char comment[172] = "Esto es una prueba - TMSA.ar";    // Max 172 bytes: telemetry_buffer(229) - telemetry_header(57)
char StatusMessage[] = "Esto es una prueba - TMSA ar"; // Se envía solo la primera vez
//*****************************************************************************

uint16_t BeaconWait = 50; // seconds sleep for next beacon (HF or VHF). This is optimized value, do not change this if possible.
uint16_t BattWait = 60;   // seconds sleep if super capacitors/batteries are below BattMin (important if power source is solar panel)
float BattMin = 4.5;      // min Volts to wake up.
float DraHighVolt = 6.5;  // min Volts for radio module (DRA818V) to transmit (TX) 1 Watt, below this transmit 0.5 Watt. Max 10v
float GpsMinVolt = 4.0;   // min Volts for GPS to wake up. (important if power source is solar panel)
float WsprBattMin = 4.5;  // min Volts for HF mradio module to transmit (TX) ~10 mW

//******************************  HF CONFIG *************************************

char hf_call[7] = "LU1MUM"; // DO NOT FORGET TO CHANGE YOUR CALLSIGN

// #define WSPR_DEFAULT_FREQ       10140200UL //30m band
#define WSPR_DEFAULT_FREQ 14097100UL // 20m band
// #define WSPR_DEFAULT_FREQ       18106100UL //17M band
// #define WSPR_DEFAULT_FREQ       21096100UL //15m band
// #define WSPR_DEFAULT_FREQ       24926100UL //12M band
// #define WSPR_DEFAULT_FREQ       28126100UL //10m band
// for all bands -> http://wsprnet.org/drupal/node/7352

// Supported modes, default HF mode is WSPR
enum mode
{
  MODE_JT9,
  MODE_JT65,
  MODE_JT4,
  MODE_WSPR,
  MODE_FSQ_2,
  MODE_FSQ_3,
  MODE_FSQ_4_5,
  MODE_FSQ_6,
  MODE_FT8
};

enum mode cur_mode = MODE_WSPR; // default HF mode

// supported other modes freq for 20m
#define JT9_DEFAULT_FREQ 14078700UL
#define FT8_DEFAULT_FREQ 14075000UL
#define JT65_DEFAULT_FREQ 14078300UL
#define JT4_DEFAULT_FREQ 14078500UL
#define FSQ_DEFAULT_FREQ 7105350UL // Base freq is 1350 Hz higher than dial freq in USB

//*******************************************************************************

//******************************  APRS SETTINGS *********************************

// do not change WIDE path settings below if you don't know what you are doing :)
uint8_t Wide1 = 1; // 1 for WIDE1-1 path
uint8_t Wide2 = 1; // 1 for WIDE2-1 path

/**
Airborne stations above a few thousand feet should ideally use NO path at all, or at the maximum just WIDE2-1 alone.
Due to their extended transmit range due to elevation, multiple digipeater hops are not required by airborne stations.
Multi-hop paths just add needless congestion on the shared APRS channel in areas hundreds of miles away from the aircraft's own location.
NEVER use WIDE1-1 in an airborne path, since this can potentially trigger hundreds of home stations simultaneously over a radius of 150-200 miles.
 */
uint8_t pathSize = 2;               // 2 for WIDE1-N,WIDE2-N ; 1 for WIDE2-N
boolean autoPathSizeHighAlt = true; // force path to WIDE2-N only for high altitude (airborne) beaconing (over 1.000 meters (3.280 feet))

boolean beaconViaARISS = false; // there are no iGates in some regions (such as North Africa,  Oceans, etc) so try to beacon via ARISS (International Space Station) https://www.amsat.org/amateur-radio-on-the-iss/

// Send aprs high precision position extension (adds 5 bytes to beacon messaage)
boolean send_aprs_enhanced_precision = true;

boolean radioSetup = false;
boolean aliveStatus = true; // for tx status message on first wake-up just once.

static char telemetry_buff[229]; // telemetry buffer; max APRS message size (256) - coord and timestamp (27)
uint16_t TxCount = 1;            // increase +1 after every APRS transmission

//*******************************************************************************

//******************************  HF SETTINGS   *********************************

#define JT9_TONE_SPACING 174  // ~1.74 Hz
#define JT65_TONE_SPACING 269 // ~2.69 Hz
#define JT4_TONE_SPACING 437  // ~4.37 Hz
#define WSPR_TONE_SPACING 146 // ~1.46 Hz
#define FSQ_TONE_SPACING 879  // ~8.79 Hz
#define FT8_TONE_SPACING 625  // ~6.25 Hz
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

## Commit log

2022-08-13 inicio de proyecto en kicad
    hice y agregué el símbolo y footprint del módulo lightaprs
    [base_bateryholder.dxf, mainboard1.kicad_pcb, mainboard1.kicad_sch]
2022-08-14 palca de baterias terminada
    [base_bateryholder.dxf, batteryboard.kicad_pcb, batteryboard.kicad_sch]
2022-08-14 comienzo mainboard
    [mainboard1.kicad_pcb, mainboard1.kicad_sch]
2022-08-22 cambio de footprint esp32 y ruteo de algunas pistas
    [mainboard1.kicad_pcb, mainboard1.kicad_sch]
2022-08-28 version final de la batery board
    [batteryboard.kicad_pcb, batteryboard.kicad_sch, batteryboard.step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]
2022-09-07 falta agregar el mosfet que revienta el globo y el dtmf
    [mainboard1.kicad_pcb, mainboard1.kicad_sch]
2022-09-25 agregué un componente de kicad
2022-10-12 agregue circuito de rotura de globo
    [mainboard1.kicad_pcb, mainboard1.kicad_sch]
2022-10-17 cosas en mainboard
    [User Library-radio-1.STEP, mainboard1.kicad_pcb, mainboard1.kicad_sch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]
2022-10-17 agregué fución que obtiene el rssi
2022-10-17 nuevo firmware en arduino
2022-10-18 mainboard terminada
    [Component3.step, footprintaprs.dxf, mainboard1.kicad_pcb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]
2022-10-18 version final de placa baterías
    [batteryboard.kicad_pcb, batteryboard.kicad_sch, batteryboard.step]
2022-10-19 actualicé el tamaño de unos pads
    [mainboard1.kicad_pcb]
2022-10-21 agregue texto para foto
    [mainboard1.kicad_pcb]
2022-10-22 cambie para tener dos señales de control distintas
    [batteryboard.kicad_pcb, batteryboard.kicad_sch]
2022-10-22 actualicé pines del esp32
    [mainboard1.kicad_pcb, mainboard1.kicad_sch]
2022-10-22 agrego funciones de gps y corrijo defines
2022-10-27 agregue pines de baterías para aprs
    [batteryboard.kicad_pcb, batteryboard.kicad_sch]
2022-10-31 importe nueva version de leo
    [mainboard1.kicad_pcb, mainboard1.kicad_sch]
2022-10-31 agegue el conector de energía separado para el aprs
    [mainboard1.kicad_pcb, mainboard1.kicad_sch]
2022-10-31 agrego el firmware custom de lightaprs
2022-11-08 quito softwareserial, envía tramas i2c
2022-11-08 agrego sensor temp externo DS18B20
2022-11-15 correcciones
    resistencias en operacionales no inversores de medición de corriente y MOSFET invertidos
    [mainboard1.kicad_pcb, mainboard1.kicad_sch]
2022-11-16 continuo firmware esp32
2022-11-18 máquina de estados desarrollada
2022-11-20 agrego comandos UART
2022-11-20 lightaprs envía coord por i2c solo si son válidas
2022-11-22 corrijo errores, aprs y xtend funcionan
    [LightAPRS-W-pico-balloon.ino, main.cpp]
2022-11-23 se corrijió i2c y se agregaron comandos
2022-11-23 corrijo db enviados por uart
2022-11-29 corrigiendo errores i2c
2022-12-01 agrego margenes de error a altura gps
    [lightaprs.cpp, main.cpp]
2022-12-06 agrego lectura y reporte y de tensión de vaterías
2022-12-12 agrego test esp32
2022-12-14 mejoras en lógica de vuelo
2022-12-15 limpio buffer de entrada lightaprs
2022-12-15 para prueba, no recibe siempre vbatesp
2023-12-21 add presentation files
    [WES0012-02_ASCII v7.3mf, mainboard1.kicad_sch]
